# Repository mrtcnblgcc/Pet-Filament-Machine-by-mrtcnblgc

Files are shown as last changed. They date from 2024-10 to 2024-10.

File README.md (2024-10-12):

# Pet-Filament-Machine-by-mrtcnblgc

Making PET filament for 3D Printer from PET bottles.

## Part List:
#### **Electronical :**
- 220V AC to 12V DC/5A power supply. 
- Arduino Pro Mini (5V, 16 Mhz).
- A4988 Step Motor Driver.
- SSD1306 OLED Display.
- 12V Heater.
- IRFZ44N Mosfet.
- 100k Ohm Thermistor.
- LM317T Voltage Regulator.
- Switch.
- Capacitors (2x4.7uF, 1x100nF).
- Resistors (1x100r, 1x330r, 5x10k, 1x1k, 1x4.7k).
- 2.54mm Male and Female Connectors.

#### **Mechanical :**
- 3D Printed parts. I'm using ecodecat3d's STL files for gear set. You can visit him/her site (https://sites.google.com/view/makeyourownecopet/inicio).
- 4x 608zz model ruller for gear set.
- Some dimensions screws and nuts.
- 3D Printer extruder set. (Heating block and nozzle) You need to expand the nozzle to 1.75mm.
- L shaped metal shelf holder for hold extruder.
- 3D Printed bottle cutter. I'm using this (https://www.thingiverse.com/thing:5442876).
- Suitable pieces of wood for the floor

## Installation 
### Mechanical Instruction
A wooden or similar base is required where you will place the gear box and heater block. First, you need to create the gear box, connect the motor to the gear box. Then, you should place the heater block in line with the gear box. I placed the power supply behind the wooden block that I used. If you want, you can place it in an independent place. You can also place the piece that we will use to cut the pet bottles on this wooden base like I did.

1.1) Placing gearbox and heater block.

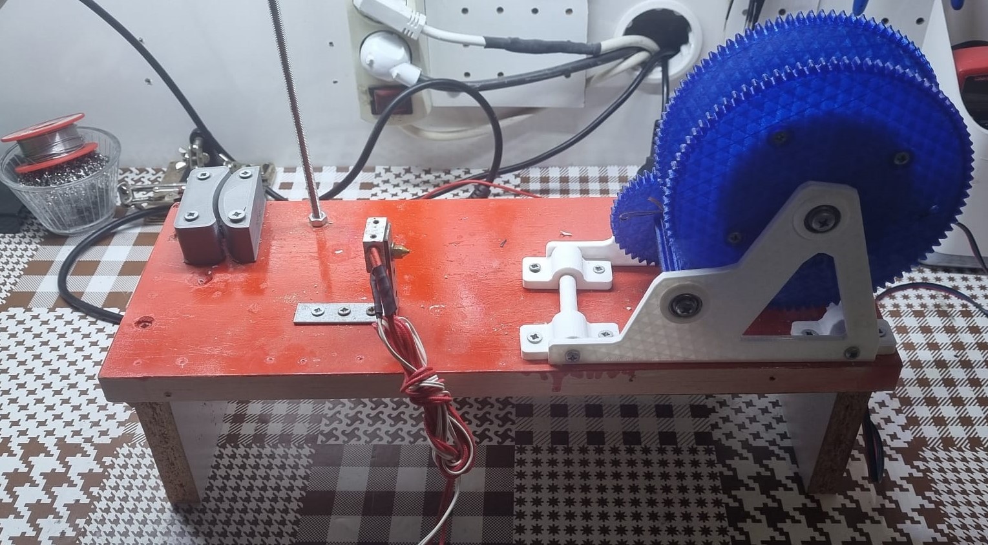
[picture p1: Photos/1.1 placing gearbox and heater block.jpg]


1.2) Placing power supply and the piece we will use to cut the PET bottles

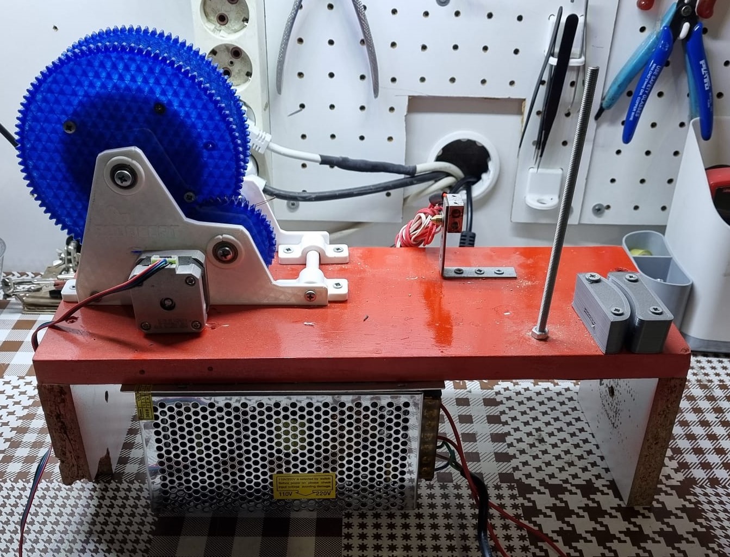
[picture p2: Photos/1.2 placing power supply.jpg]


### Electronical Instruction
I installed the electronic card on a perforated board. However, a printed circuit board can also be produced. The schematic is as follows:

Schematic;

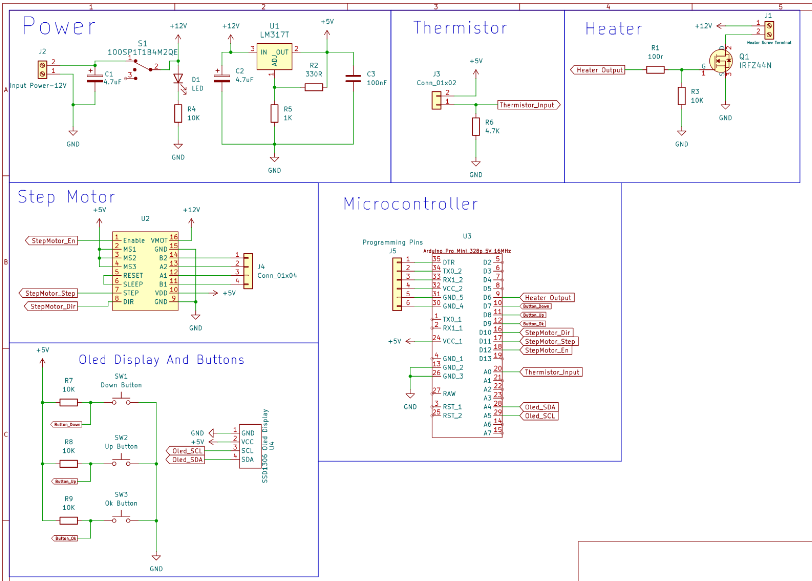
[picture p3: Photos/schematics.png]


Creating the circuit on a perforated board;

2.1)Electronic circuit and OLED screen

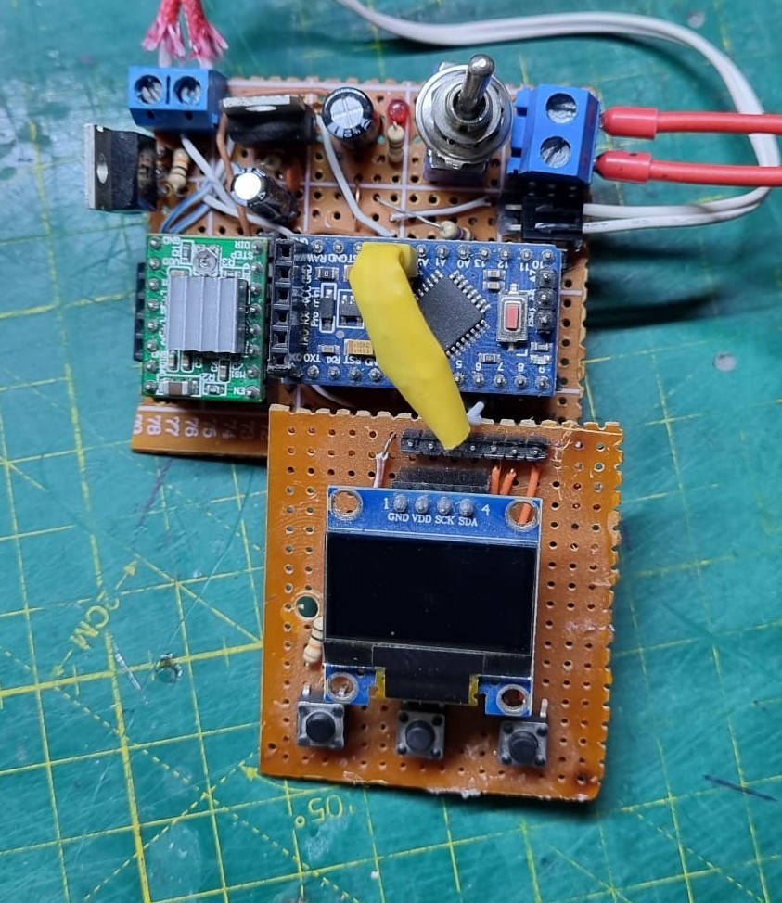
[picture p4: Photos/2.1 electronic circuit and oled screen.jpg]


2.2) Behind the circuit;

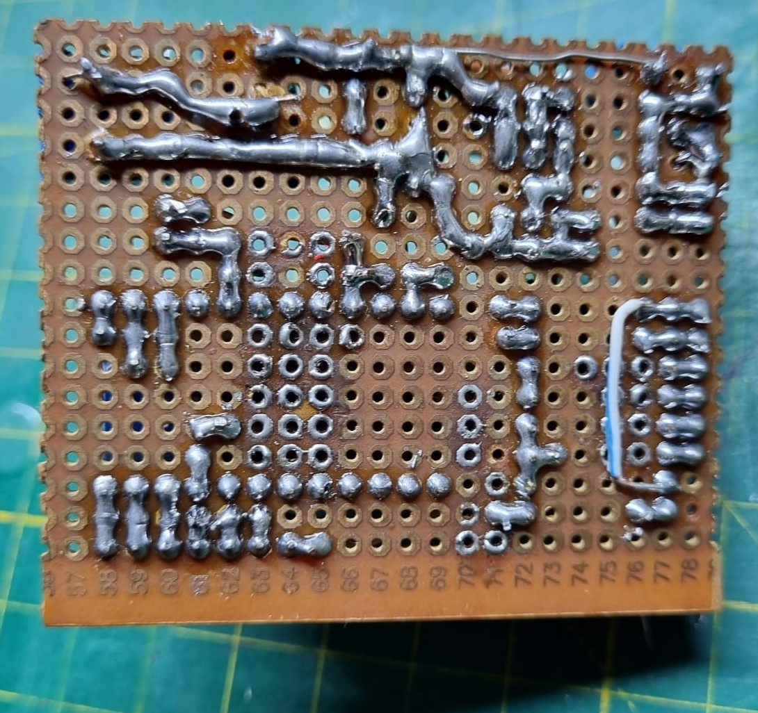
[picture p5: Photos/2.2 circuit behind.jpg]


3.1) Initial menu view;

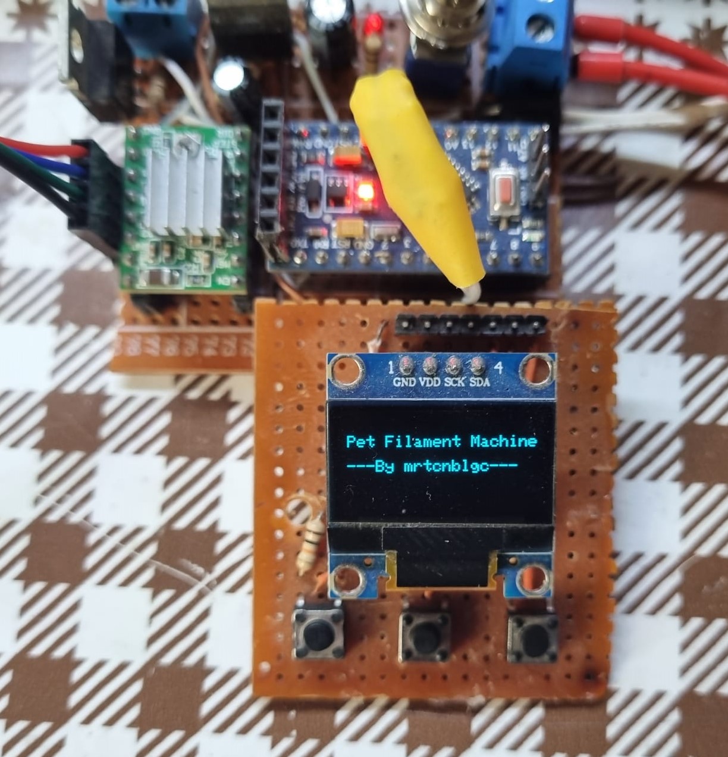
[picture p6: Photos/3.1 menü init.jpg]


3.2) In general menu;

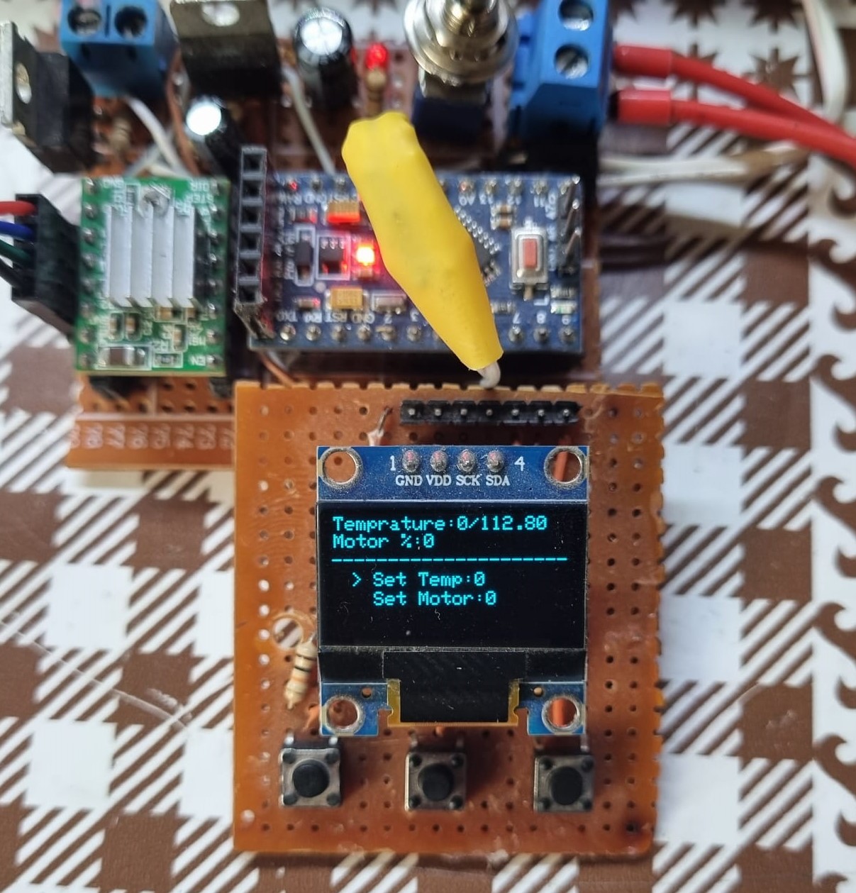
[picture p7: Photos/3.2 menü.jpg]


The right arrow button is the "OK" button. The left button is the "DOWN" button and the middle button is the "UP" button. 

To operate the heater at the desired value, press the "OK" button once while the ">" symbol is on "Set Temp". There will be no change on the screen. However, when you press the "UP" button, the value will increase by ten. Similarly, when you want to decrease, press the "DOWN" button. The value will decrease by ten. When you reach the desired value, you will return to the main menu when you press the "OK" button.

You must do the same to operate the step motor and adjust its speed. You must press the "UP" and "Down" buttons to navigate between "Set Temp" and "Set Motor" in the menu.

# Process
If you have installed mechanical and electronical things you are ready process of making filament from PET, congraculations! :)

First, you need cut the top and bottom side of the bottle. After this, you will need to make a small splinter-shaped cut on the end of the bottle to be able to insert it into the plastic bottle slicer.

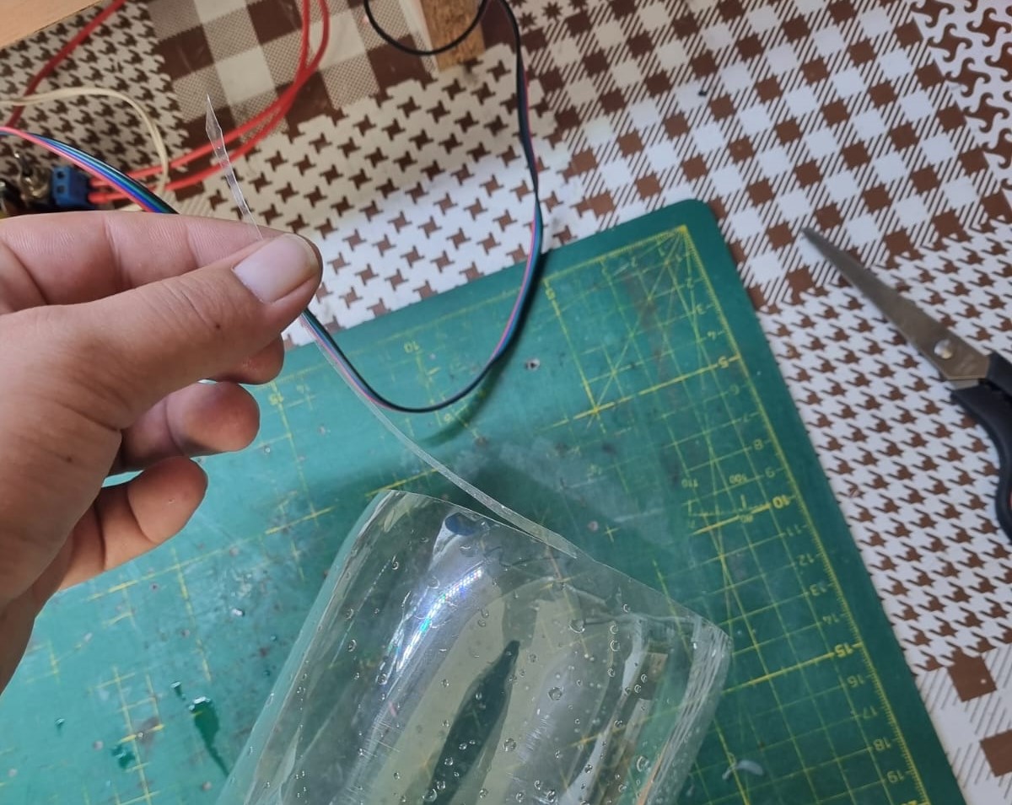
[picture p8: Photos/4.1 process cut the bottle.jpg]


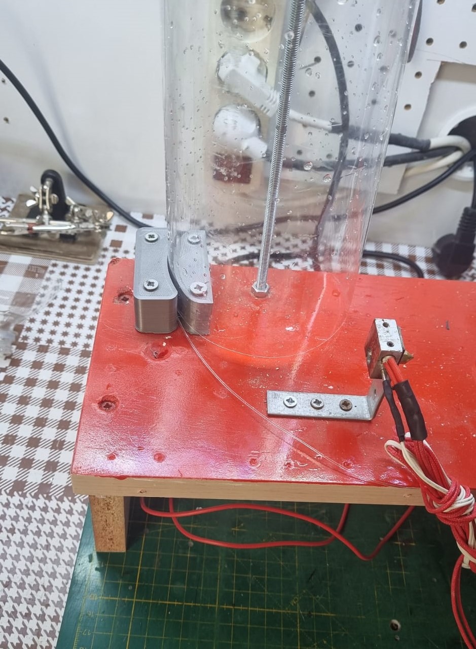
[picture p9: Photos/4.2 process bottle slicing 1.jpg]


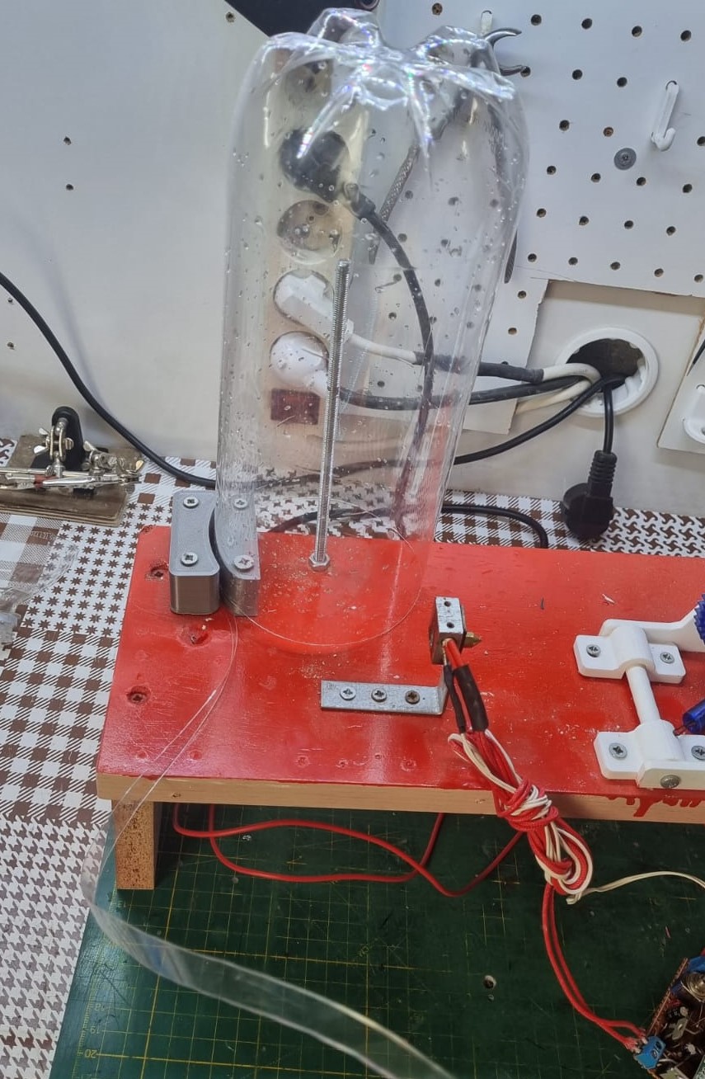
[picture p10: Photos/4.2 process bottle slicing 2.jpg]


And final result;

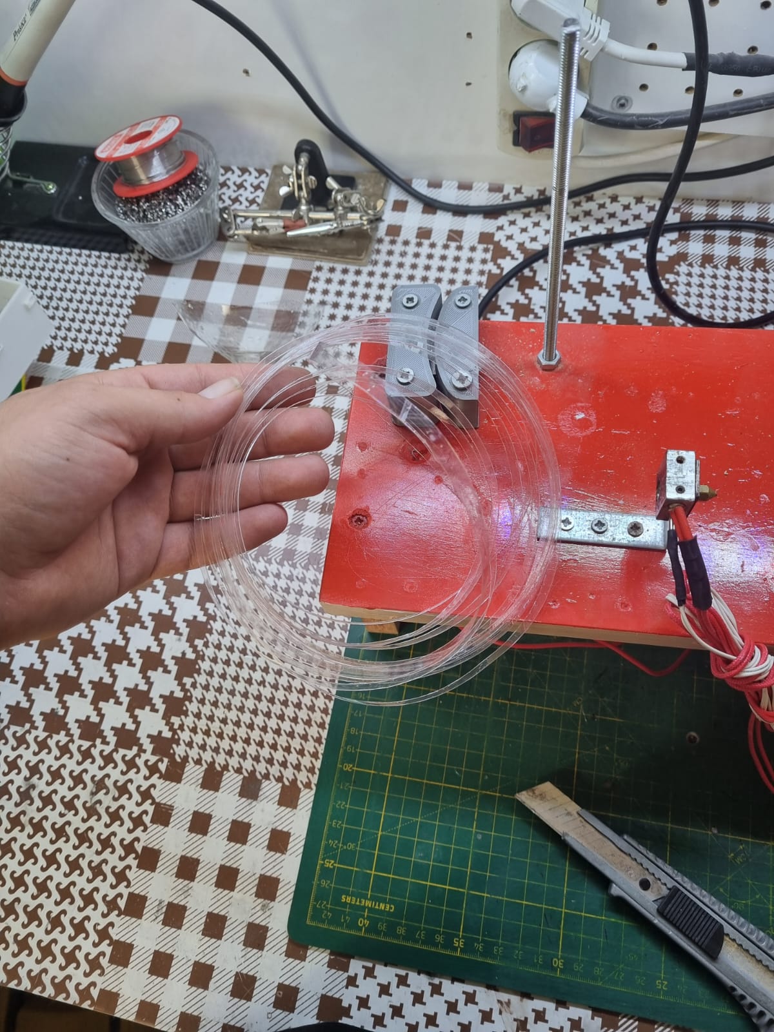
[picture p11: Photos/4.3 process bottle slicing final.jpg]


After slicing the bottle, we slice the PET thinner. Then, while the heater is cold, we pass it through the heater. 



After passing, we heat the heater between 180°C and 200°C. When the heater reaches the desired temperature, we compress the filament that comes out with a pipe-like object to the rope connected to the gear. After this process, we start the motor and let it wind. And here is our filament!

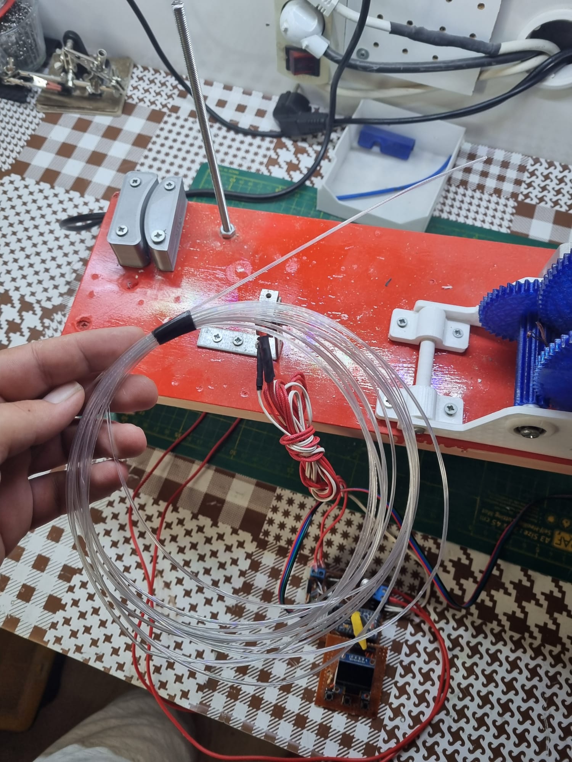
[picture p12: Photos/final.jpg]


Video link; [click here](https://www.youtube.com/watch?v=tgluLH4R5xo)

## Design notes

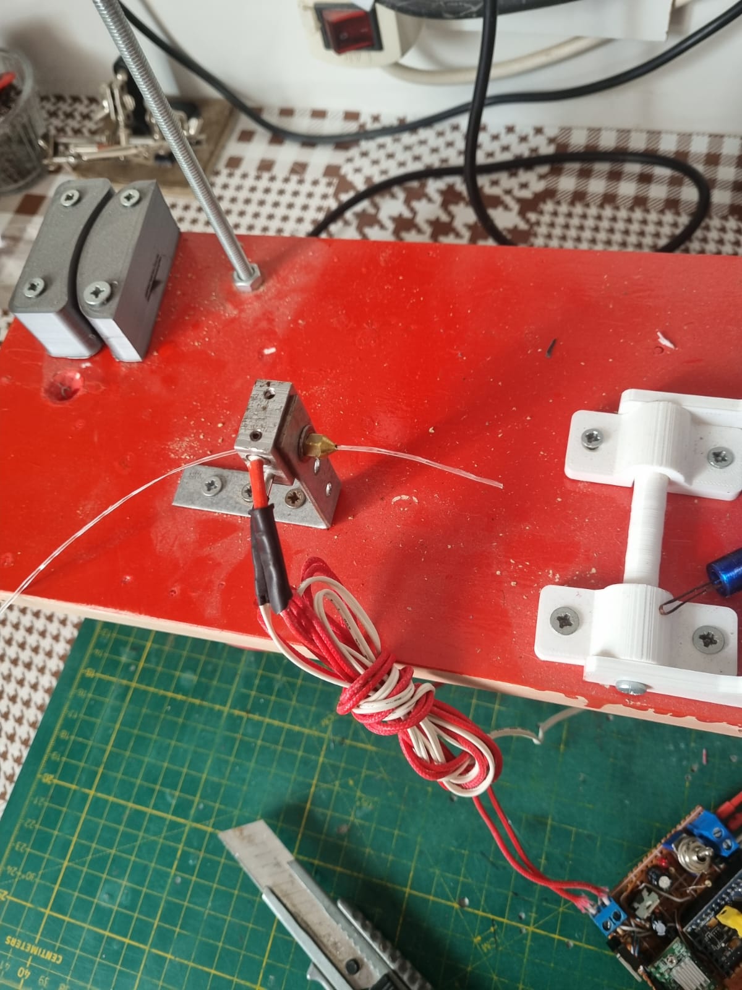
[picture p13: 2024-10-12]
Photos/4.4 inserting sliced pet into the heater.jpg

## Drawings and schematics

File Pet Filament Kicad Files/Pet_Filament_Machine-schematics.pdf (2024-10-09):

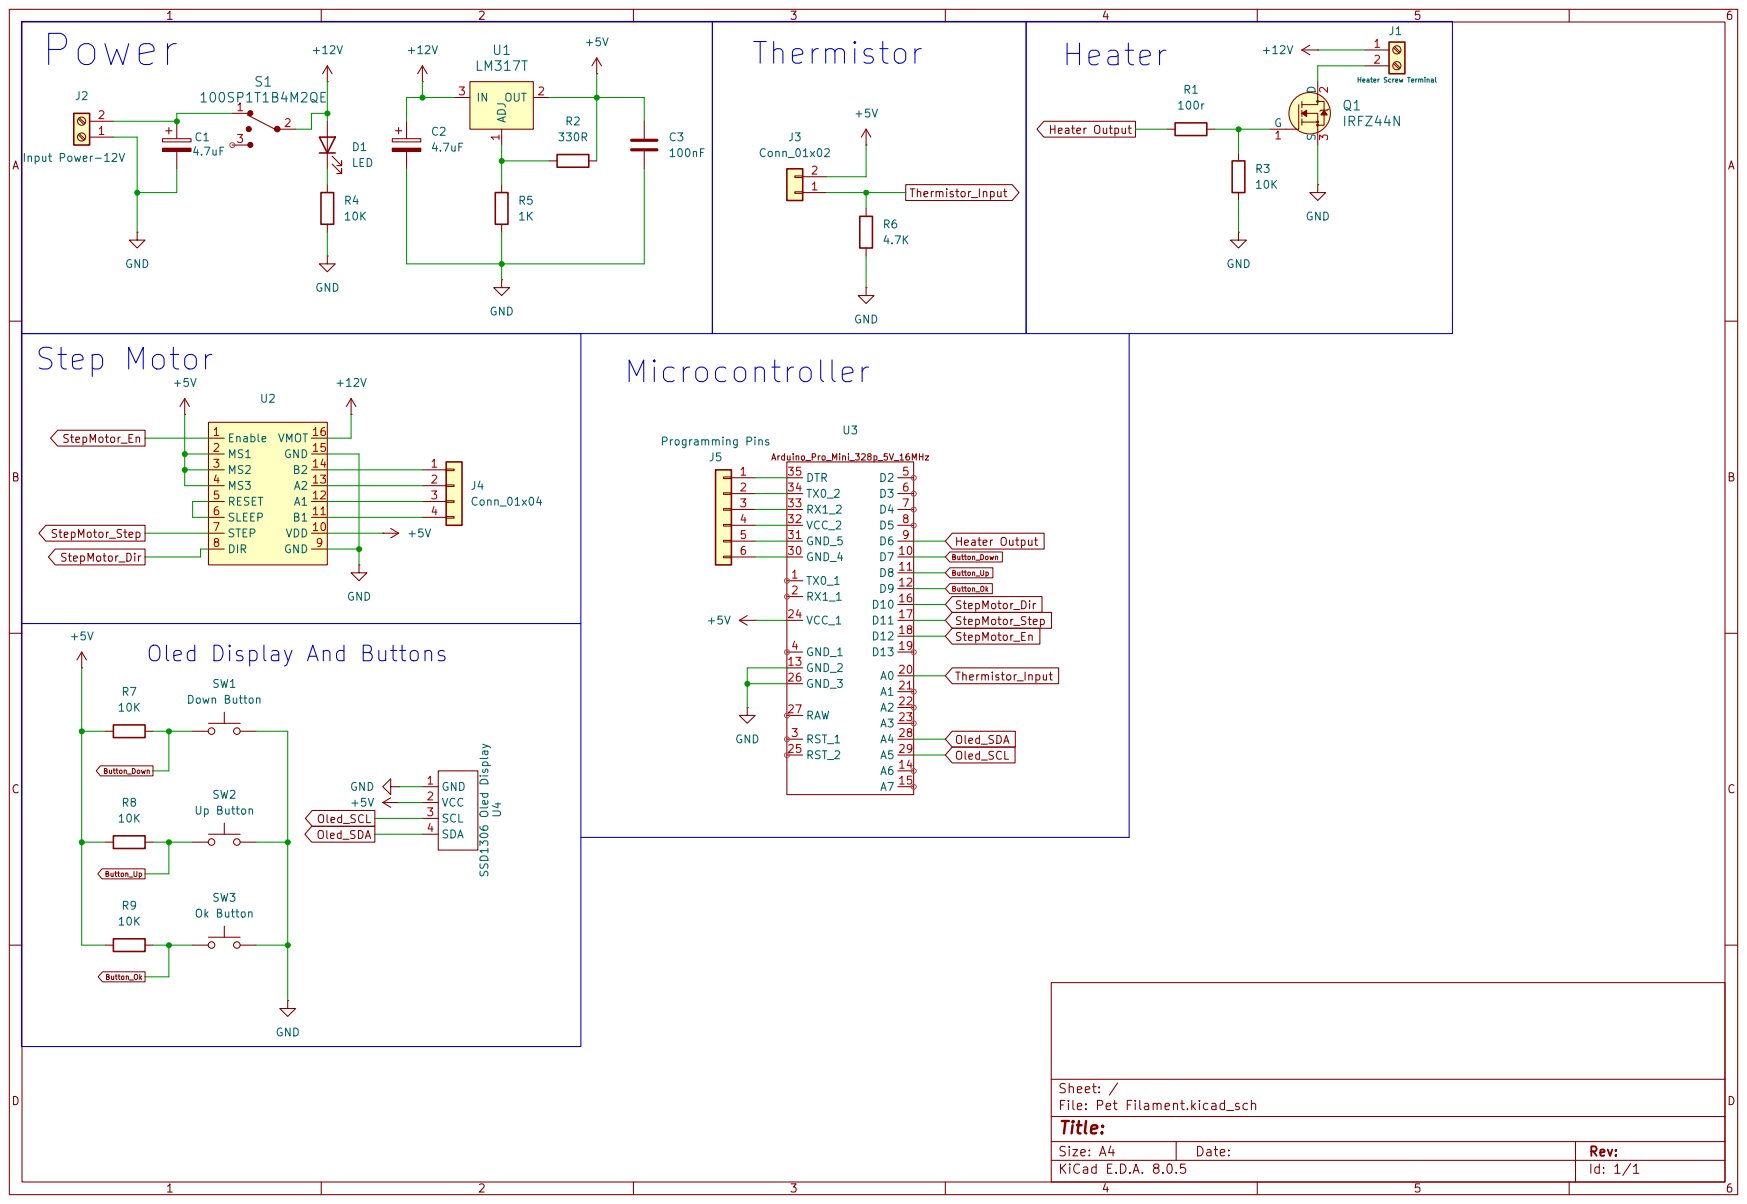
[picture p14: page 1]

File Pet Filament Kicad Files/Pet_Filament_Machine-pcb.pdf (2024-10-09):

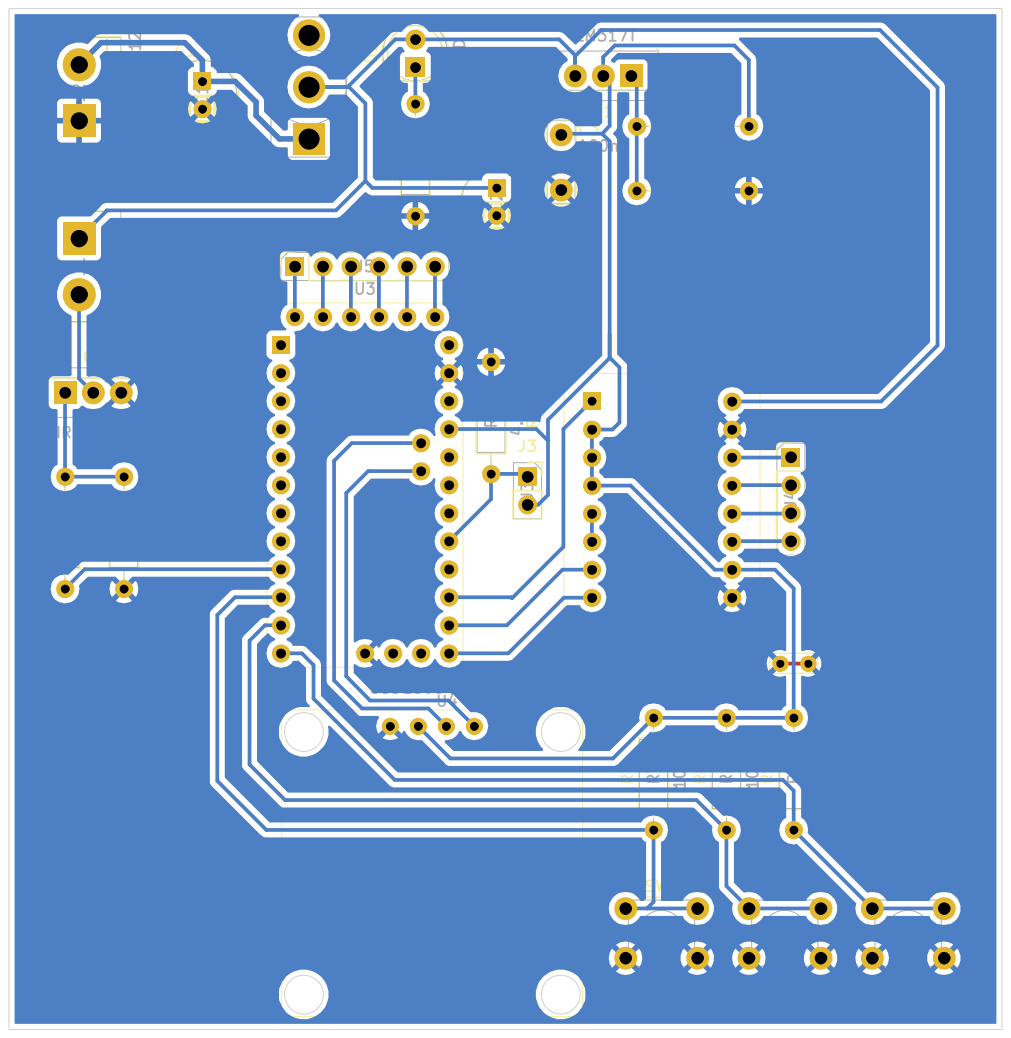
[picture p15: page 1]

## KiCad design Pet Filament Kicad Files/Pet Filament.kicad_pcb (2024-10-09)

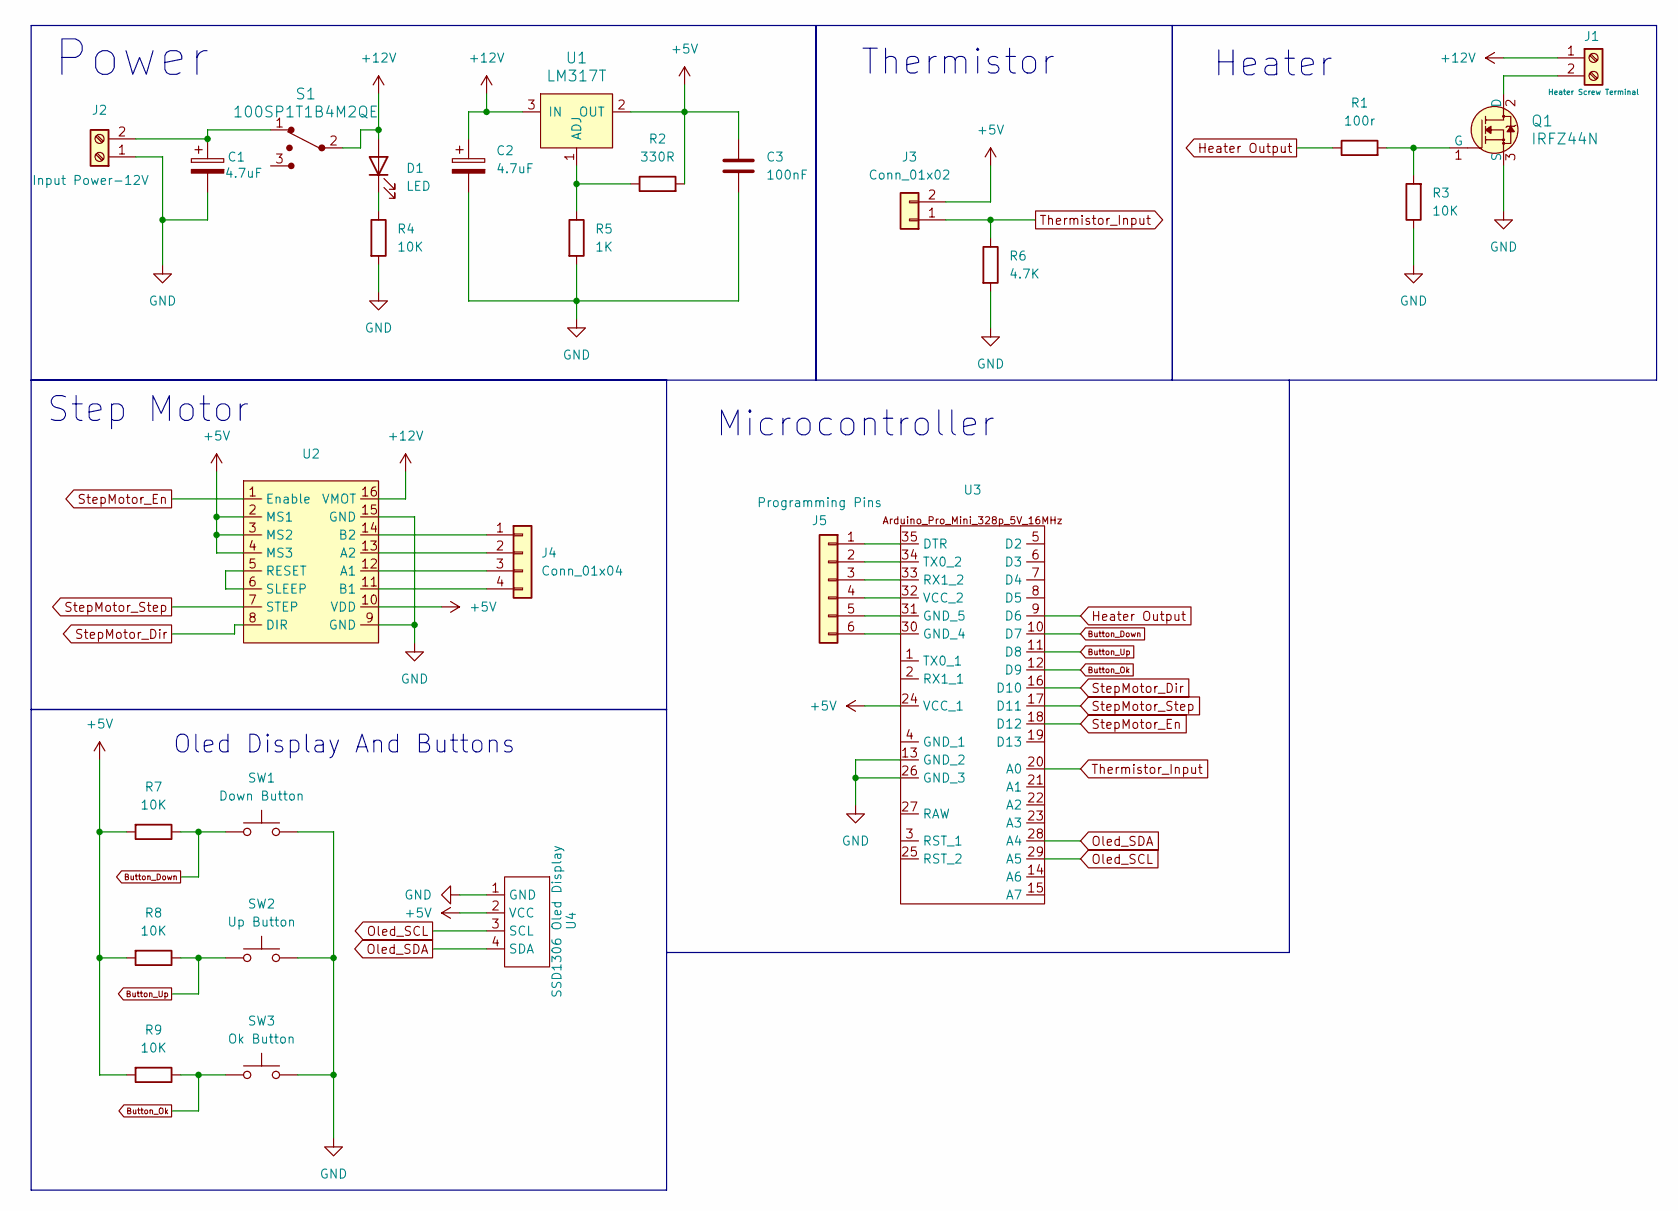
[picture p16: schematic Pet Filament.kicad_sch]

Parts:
C1, C2: 4.7uF; CP_Radial_D6.3mm_P2.50mm
C3: 100nF; C_Disc_D7.5mm_W2.5mm_P5.00mm
D1: LED; LED_D5.0mm_FlatTop
J1: Heater Screw Terminal; TerminalBlock_bornier-2_P5.08mm
J2: Input Power-12V; TerminalBlock_bornier-2_P5.08mm
J3: Conn_01x02; PinSocket_1x02_P2.54mm_Vertical
J4: Conn_01x04; PinHeader_1x04_P2.54mm_Vertical
J5: Programming Pins; PinSocket_1x06_P2.54mm_Vertical
Q1: IRFZ44N; TO-220-3; MPN IRF540NPBF
R1: 100r; R_Axial_DIN0207_L6.3mm_D2.5mm_P10.16mm_Horizontal
R2: 330R; R_Axial_DIN0207_L6.3mm_D2.5mm_P10.16mm_Horizontal
R3, R4, R7, R8, R9: 10K; R_Axial_DIN0207_L6.3mm_D2.5mm_P10.16mm_Horizontal
R5: 1K; R_Axial_DIN0207_L6.3mm_D2.5mm_P10.16mm_Horizontal
R6: 4.7K; R_Axial_DIN0207_L6.3mm_D2.5mm_P10.16mm_Horizontal
S1: 100SP1T1B4M2QE; Toggle_Switch_100SP1T1B4M2QE; MPN 100SP1T1B4M2QE
SW1: Down Button; SW_PUSH_6mm
SW2: Up Button; SW_PUSH_6mm
SW3: Ok Button; SW_PUSH_6mm
U1: LM317T; TO-220-3; MPN LM317T
U2: A4988_Board
U3: Arduino_Pro_Mini_5V_Board
U4: SSD1306 Oled Display; Lib-SSD1306-Oled-I2C-128x64

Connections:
+5V: C3.1, J3.2, R2.2, R7.2, R8.2, R9.2, U1.2 (OUT), U2.2 (MS1), U2.3 (MS2), U2.4 (MS3), U2.10 (VDD), U3.24 (VCC_1), U4.2 (VCC)
+12V: C2.1, D1.2 (A), J1.1, S1.2 (Com), U1.3 (IN), U2.16 (VMOT)
Button_Down: R7.1, SW1.1, U3.10 (D7)
Button_Ok: R9.1, SW3.1, U3.12 (D9)
Button_Up: R8.1, SW2.1, U3.11 (D8)
GND: C1.2, C2.2, C3.2, J2.1, Q1.3 (S), R3.1, R4.2, R5.2, R6.2, SW1.2, SW2.2, SW3.2, U2.9 (GND), U2.15 (GND), U3.13 (GND_2), U3.26 (GND_3), U4.1 (GND)
Heater Output: R1.1, U3.9 (D6)
unnamed: D1.1 (K), R4.1
unnamed: J1.2, Q1.2 (D)
unnamed: C1.1, J2.2, S1.1
unnamed: J4.1, U2.14 (B2)
unnamed: J4.2, U2.13 (A2)
unnamed: J4.3, U2.12 (A1)
unnamed: J4.4, U2.11 (B1)
unnamed: J5.1, U3.35 (DTR)
unnamed: J5.2, U3.34 (TX0_2)
unnamed: J5.3, U3.33 (RX1_2)
unnamed: J5.4, U3.32 (VCC_2)
unnamed: J5.5, U3.31 (GND_5)
unnamed: J5.6, U3.30 (GND_4)
unnamed: Q1.1 (G), R1.2, R3.2
unnamed: R2.1, R5.1, U1.1 (ADJ)
unnamed: U2.5 (RESET), U2.6 (SLEEP)
Oled_SCL: U3.29 (A5), U4.3 (SCL)
Oled_SDA: U3.28 (A4), U4.4 (SDA)
StepMotor_Dir: U2.8 (DIR), U3.16 (D10)
StepMotor_En: U2.1 (Enable), U3.18 (D12)
StepMotor_Step: U2.7 (STEP), U3.17 (D11)
Thermistor_Input: J3.1, R6.1, U3.20 (A0)

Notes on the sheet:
Heater
Power
Thermistor
Step Motor
Microcontroller
Oled Display And Buttons

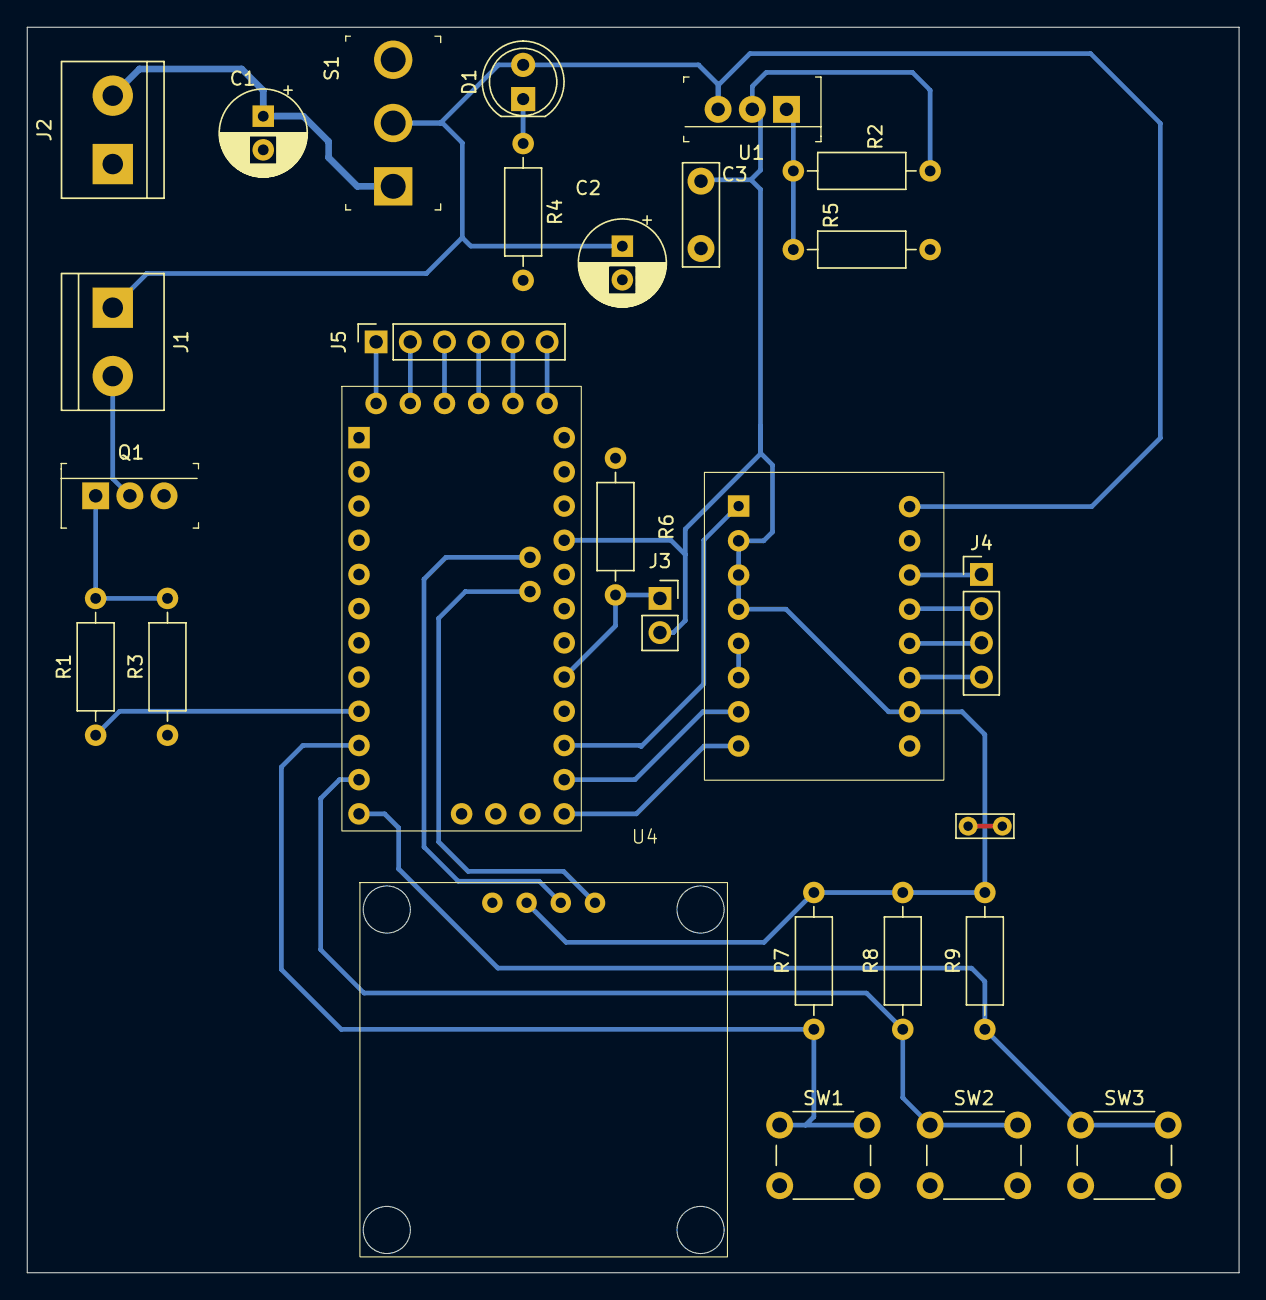
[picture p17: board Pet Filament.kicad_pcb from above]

Board: 2 copper layers, 90.0 x 92.5 mm, 27 parts (0 on the bottom side), 29 nets.

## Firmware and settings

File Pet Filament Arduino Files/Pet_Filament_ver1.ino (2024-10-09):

#include "drv_pid.h"
#include "drv_thermistor.h"
#include "drv_menu.h"
#include "drv_step_motor.h"


//#define setpoint_in_c 150
const float kp = 25;
const float ki = 0.5;
const float kd = 0.001;

const int thermistor_pin = A0;
int output_pin = 6;
double output=0;

float real_temp=0;
double error;

int get_temp_value=0;
int get_motor_velo=0;


void setup() {
  Serial.begin(9600);
  drv_step_motor_init();
  drv_menu_init();
  delay(2500);
}

void loop() {

  get_temp_value = drv_menu_get_temp();
  real_temp = get_thermistor_value(thermistor_pin);

  drv_menu_update(real_temp);

  error= (get_temp_value) - (real_temp) ;
  output=pid(kp, ki, kd, error);
  analogWrite(output_pin, output);

  //drv_step_motor_write (get_motor_velo);
  get_motor_velo = drv_menu_get_velo();
  drv_step_motor_write(get_motor_velo);


  // Monitoring values 
  
  Serial.print("Setpoint: "); Serial.print(get_temp_value);
  Serial.print(" *** ");
  Serial.print("Real Temparute: "); Serial.print(real_temp);
  Serial.print(" *** ");
  Serial.print("Output: "); Serial.print(output);
  Serial.print(" *** ");
  Serial.print("Motor Value: "); Serial.print(get_motor_velo);
  Serial.println(" *** ");
  
  
  //Serial.print("Error:  "); Serial.println(error);
  //Serial.print("Output: "); Serial.println(output);
  //Serial.println("");
  //delay(1000);

}

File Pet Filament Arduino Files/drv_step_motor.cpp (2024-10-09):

#include "drv_step_motor.h"
#include <Arduino.h>

const int stepPin = 11; // Step pinini tanımlayın
const int dirPin = 10;  // Direction pinini tanımlayın
const int enPin= 12;  // Enable pinini tanımlayın


void drv_step_motor_init() {
  //Serial.begin(9600);
  pinMode(stepPin, OUTPUT);
  pinMode(dirPin, OUTPUT);
  pinMode(enPin, OUTPUT);
  
  digitalWrite(dirPin, HIGH);
  digitalWrite(enPin, HIGH);

}

void drv_step_motor_write (int speed) {

  if( speed == 0) {
    digitalWrite(enPin, HIGH);

  }

  else if ( 0<speed<100 ) {
  digitalWrite(enPin, LOW);
  TCCR2A |= (1<<WGM20)  | (1<<COM2A0) | (1<<COM2B0) ;
  TCCR2B |= (1<<WGM22) |  /*(1<<CS20) |   (1<<CS21)  |*/  (1<<CS22) ;

  speed=map(speed,0,100,0,255);
  OCR2A = 255 - speed;
  }
  else if (speed == 100) {
    speed=99;
  }

}
